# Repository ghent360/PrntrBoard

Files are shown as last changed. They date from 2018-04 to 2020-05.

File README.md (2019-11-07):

Prntr Board V1
======================
## *Deprecated*
**This project has run it's course. Most of the features are complete and there is little I can improve further. I have switched my focus to the [V2 design](https://github.com/ghent360/PrntrBoardV2).**

------------------

PrntrBoard is a 3D printer controller board designed to work with STM32 NUCLEO dev kits. The current version (V1) supports NUCLEO-64 series kits. The design is being developed on F446-RE kit, but other models could work as well. IMO the STM32F446 NUCLEO-64 kit offers very good performance (180MHz CPU) for the price ($15).

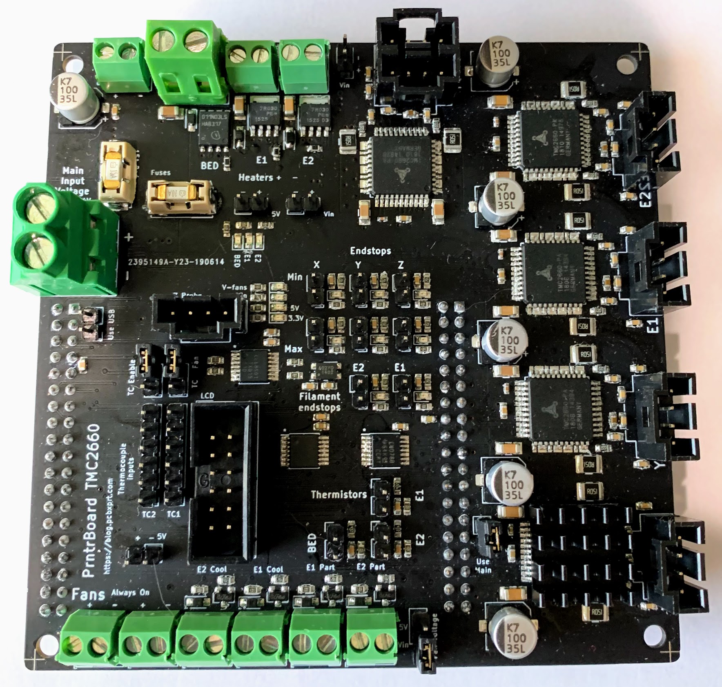
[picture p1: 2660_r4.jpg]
Picture of Rev2 Kicad Rendering

Some features of the board:
-----
  + 5x Trinamic super quiet drivers (TMC2130, TMC2660 or TMC2209)
  + Marlin 2.0 firmware
  + (2+2) controllable fans and 2x "always on" fan connectors
  + 3x min and max endstops for the x, y and z axis
  + 2x end stops for fillament end detection
  + SPI or I2C display connector for ST7735 or SSD1306 screen + one button and rotary encoder
  + Dual thermocouple connectors (for MAX31866, MAX31855 or MAX6675 boards)
  + Input voltage (Vin): 12-24V
  + selectable fan voltage (5V or Vin)

Because the NUCLEO-64 has limited number of IO pins, some compromises had to be made:
  + ~~No sd-card~~ (sd-card is added using new NUCLEO-64 compatible board)
  + The thermocouple connectors share pins with the E0 and E1 cool fan controls. You'll have to decide to use one or the other via jumpers on the board. Most printers I've seen come with "always on" extruder fans, the choice seemed like a worthy sacrifice.

Generic shortcuts I don't plan to improve:
------
  + ~~5V power supply is external. These are available from various resellers and fairly cheap - less than $1. No need to waste board layout space and component count.~~ (this has beed addresses with the new NUCLEO-64 compatible daugherboard)
  + Heated bed MOSFET - large heated beds consume a lot of power and it is challenging to provision the design for > 20A current (there is simply not enough copper space on the board to support this current). External heated bed MOSFETs are very affordable < $10 and support 20A-40A with no issues. If you have large heated bed - use external MOSFET or SSR.

Details
------
I use the daily build of KiCad (soon to be released V6) - let me know if you have trouble opening the files.

The current PCB desing is using 4 layer board, 6/6 mil track width/clearance, 12 mil min via hole size and 20 mil via diameter.

There are tree active branches:
  + tmc2130 - the board design for TMC2130 drivers
  + tmc2130-redesign - redesign of the TMC2130 branch with the nucleo board flipped
  + tmc2660 - the board design for TMC2660 drivers
  + tmc2209 - the board design for TMC2209 drivers

TMC2130 and TMC2660 PCB designs use the QFP version of the driver ICs, because they can handle a bit more power. The TMC2209 is available only in QFN package.

Status
------
TMC2130 version is table and been running for over a year. TMC2660 is being tested at the moment. Prototypes of the TMC2209 are being made.

old status:
I've been running a prototype of this board for a few months now and I'm very happy with the board stability. I'm trying to figure out how to make these at scale.

I have made prototypes of the TMC2130 board design (rev0) - the board has a few bugs, that are corrected in the rev1 version. Rev0 did not have LCD screen, it was added in Rev1. I'm trying to work-out the thermal design issues.
Rev1 board have been ordered and the dev branch is now switched to Rev2. The thermocouple connectors are added Rev2.
Rev2 borads have been ordered. The current working board is rev3. Added 2 more pins to the LCD connector
for the rotary encoder input. I also re-connected the E1 and E0 CS pins, so the LCD pins can be connected
to the hardware I2C pins. This way one can use SPI or I2C screens.

This branch is a redesign of the TMC2130 board. The main difference is that the NUCLEO board is flipped in a more natural position. In addition I'm now using a dedicated ground plane, larger heatsink areas for the mosfets. I'm much happier with the thermal layout of this branch.

The NUCLEO-64 board was limiting the design in many ways. I have a replacement board using STM32F407VE. This is 100 pin part. The new daughter board is the same form factor as the NUCLEO-64. It adds SPI EEPROM as well as native USB interface and micro SD-Card socket. The new board also has enough space for 24V to 5V buck converter, so power supply can beintegrated.

Tested circuits:
  + Heater control
  + Thermistor input
  + Fan control
  + Motor driver control
  + Z probe
  + End stops
  + Thermocuple interface (tested MAX31855 with Smoothieware)
  + LCD interface (tested REPRAP discount full graphics controller - the panel has issues
  sharing the SPI port with the TMC drivers. Could be solved with adapter board with extra AND gate)

Circuits that need verification:
  + Stall guard alert from the motor driver

Software
------

The software for the board is a clone of Marlin at [bugfix-2.0.x branch](https://github.com/ghent360/Marlin/tree/bugfix-2.0.x/ "Github.com") of my repository. It is quite usable. I keep it relatively in sync with the Marlin branch. *Note: there are other branches of Marlin, only the bugfix-2.0.x supports the STM32 microcontroller.*

Marlin is using Adruino IDE or Platform IO. I personally had issues with Platform IO not supporting the STM32F4 board, so I use Arduino version 1.8.5. To compile the firmware code you would need to install the [STM32 Arduino port](https://github.com/stm32duino/Arduino_Core_STM32 "www.stm32duino.com").

I'm also porting [Smoothieware](http://smoothieware.org) V1 to the board. So far I got the heater control and the stepper drivers working. My smoothie port is available [here](https://github.com/ghent360/Smoothieware-STM32F4 "Gitgub.com"). Please not the Smoothie port is not ready yet (there is an issue with the ADC). I have done only minimal tests so far.

Visit [my blog](https://blog.pcbxprt.com/) for status updates on the development of the board.

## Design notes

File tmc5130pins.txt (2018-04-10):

1 TST_MODE
2 CLK
3 ~CS
4 SCK
5 SDI
6 N/C
7 SDO
8 STEP
9 DIR
10 VCC_IO
11 SD_MODE
12 SPI_MODE
13 GNDP
14 N/C
15 OB1
16 N/C
17 BRB
18 N/C
19 OB2
20 N/C
21 VS
22 N/C
23 ENCN_DCO
24 ENDB_DCEN
25 ENCA_DCIN
26 DIAG0
27 DIAG1
28 SWSEL
29 DRV_ENN
30 AIN_REF
31 N/C
32 GNDA
33 5VOUT
34 VCC
35 CPO
36 N/C
37 CPI
38 VCP
39 VSA
40 VS
41 N/C
42 OA2
43 N/C
44 BRA
45 N/C
46 OA1
47 N/C
48 GNDP
49 PAD

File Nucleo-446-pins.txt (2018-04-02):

1 PC10
2 PC11
3 PC12
4 PD2
5 VDD
6 E5V
7 BOOT0
8 GND
9 NC
10 NC
11 NC
12 IOREF
13 PA13
14 ~RESET
15 PA14
16 3.3v
17 PA15
18 5V
19 GND
20 GND
21 PB7
22 GND
23 PC13
24 VIN
25 PC14
26 NC
27 PC15
28 PA0
29 PH0
30 PA1
31 PH1
32 PA4
33 VBAT
34 PB0
35 PC2
36 PC1
37 PC3
38 PC0
39 PC9
40 PC8
41 PB8
42 PC6
43 PB9
44 PC5
45 AVDD
46 U5V
47 GND
48 NC
49 PA5
50 PA12
51 PA6
52 PA11
53 PA7
54 PB12
55 PB6
56 NC
57 PC7
58 GND
59 PA9
60 PB2
61 PA8
62 PB1
63 PB10
64 PB15
65 PB4
66 PB14
67 PB5
68 PB13
69 PB3
70 AGND
71 PA10
72 PC4
73 PA2
74 NC
75 PA3
76 NC

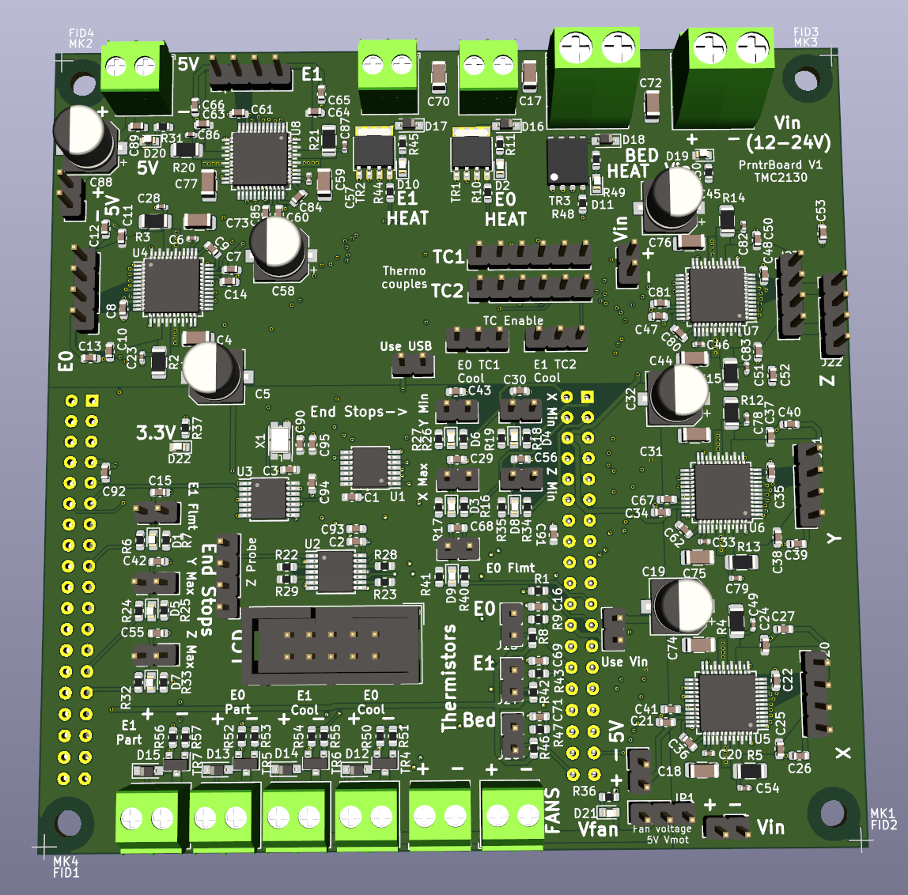
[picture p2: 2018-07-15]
Rev2_2.png

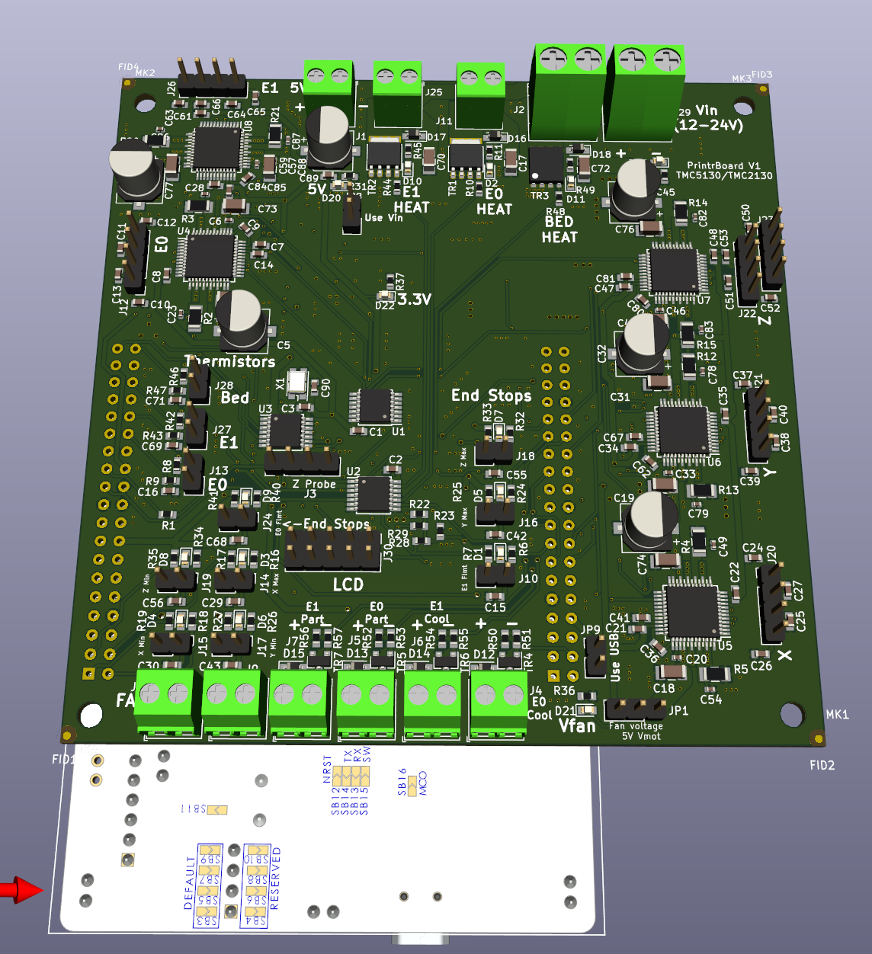
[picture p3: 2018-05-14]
Rev1_1.png

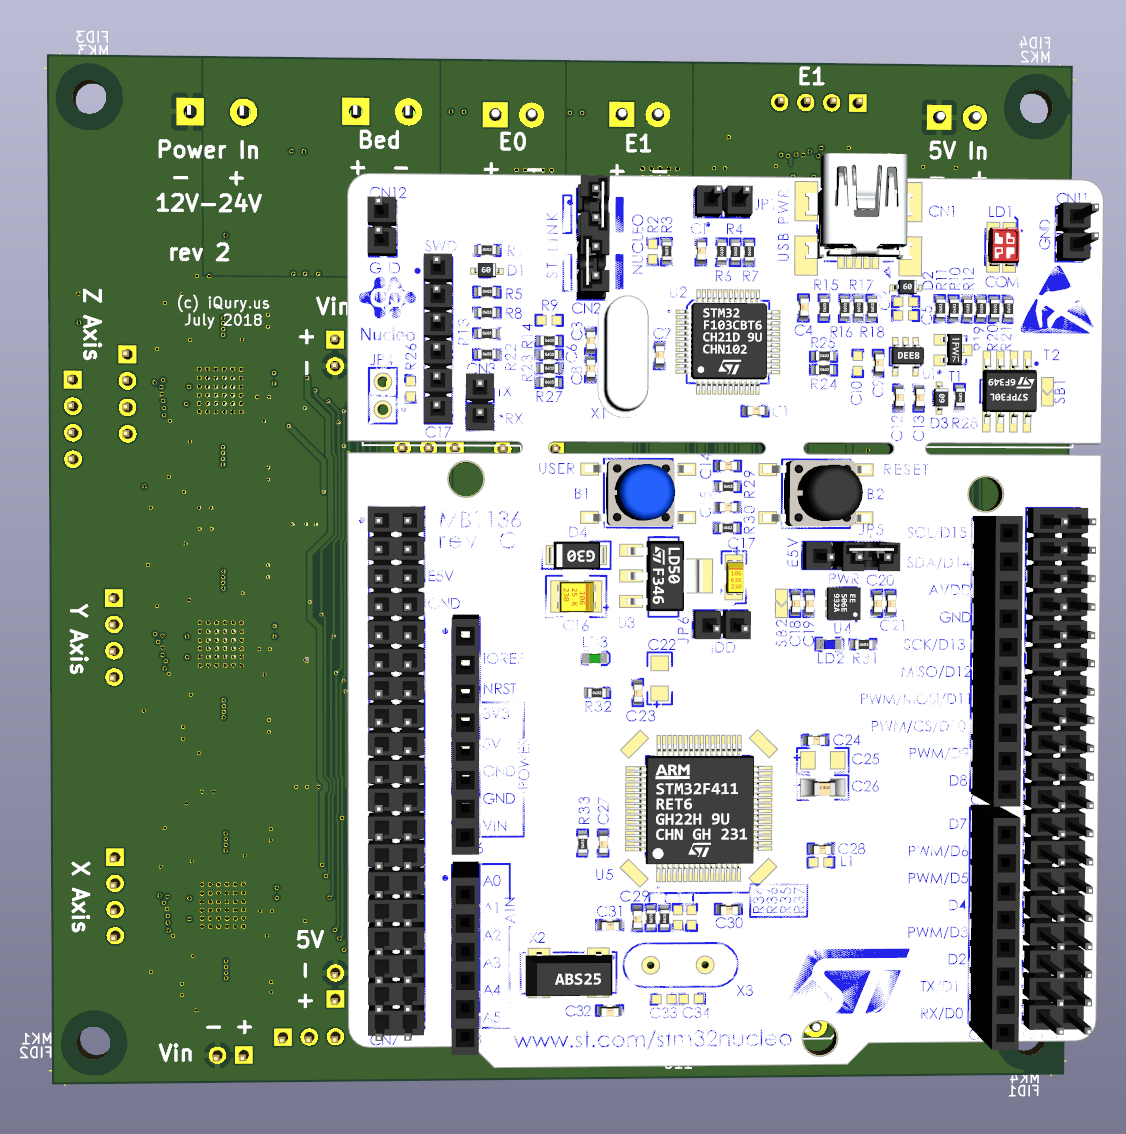
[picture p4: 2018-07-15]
Rev2_1.png

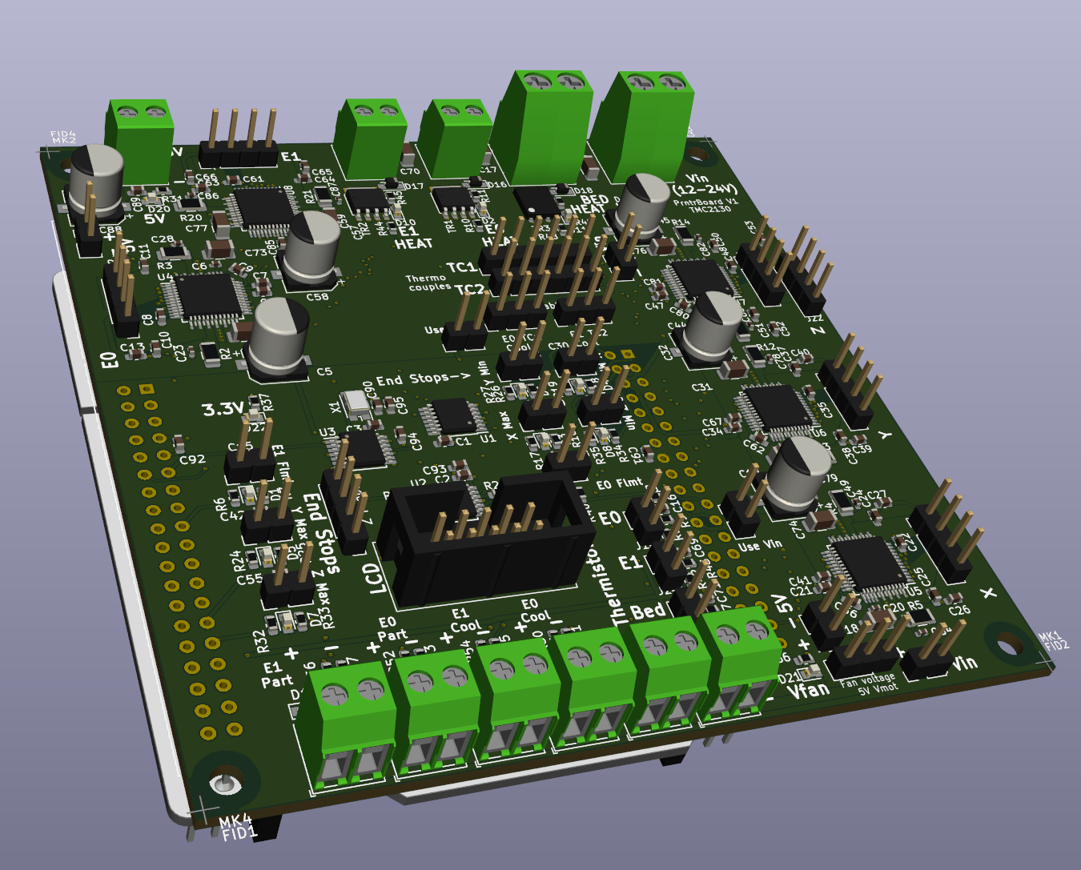
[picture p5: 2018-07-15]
Rev2_3.png

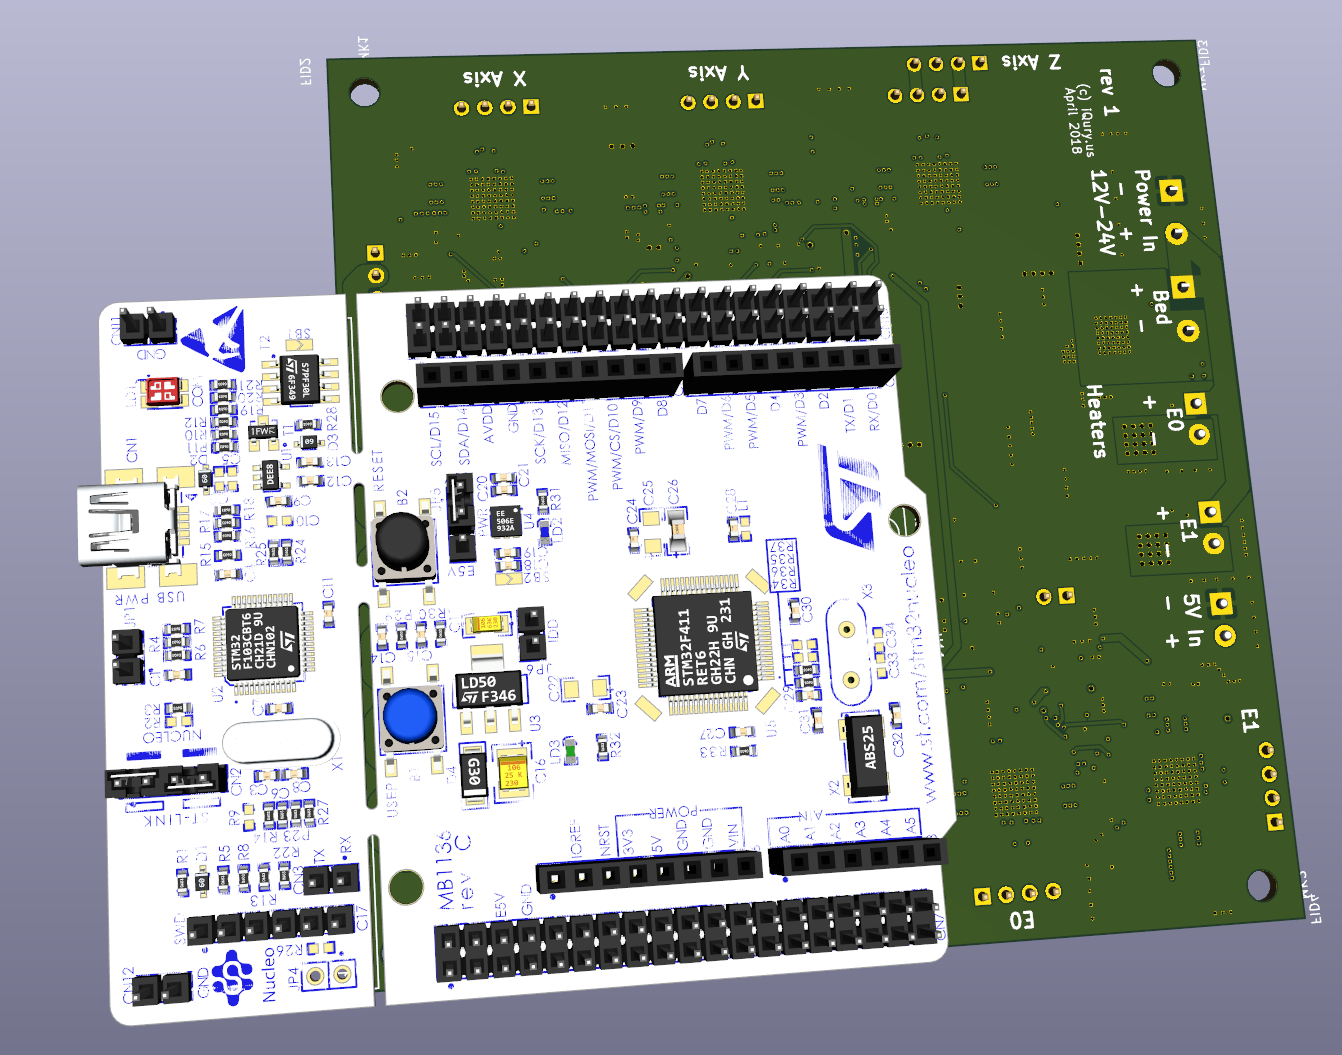
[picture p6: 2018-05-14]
Rev1_2.png

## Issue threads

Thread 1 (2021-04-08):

some advices

chinamore, 2021-04-08:
This version has the biggest problem. I guess no one except you dares to copy this board. My idea is very simple. You can clear all the TMC2660 and use a double-layer board layout, which will save a lot of cost. Provide 4 signals for each axis of the closed-loop printer: P+D+E+GND, which will greatly facilitate players who use external drives

ghent360, 2021-04-08:
Could you elaborate what problem you are referring to?
I do not believe a double layer board would provide sufficient cooling.
Also the cost difference of a double vs 4 layer board is minimal at 10x10cm
size (jlcpcb.com).

~V

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

M10CUBE, 2021-12-05:
Hi @ghent360
Some time ago we made a hardware platform called M10CUBE
https://hackaday.io/project/171770-m10cube
https://gitlab.com/m10cube/m10
A few days ago I ported to M10CUBE from maker @terjeio a similar to yours (NUCLEO64) hardware but for CNC control
https://github.com/terjeio/CNC_Breakout_Nucleo64/issues/3
I know you made a new version of the REPRAP controller but I like more the NUCLEO idea. More flexible and extremely cheap.
One goal now I am looking is to make a common controller for REPRAP and CNC.
Having all I/Os needed of the main board and use M10CUBE I/O modules

I have explained the concept here:
https://github.com/grblHAL/RP2040/discussions/3#discussioncomment-1752487
I am watching this in your you tube channel as well
Thanks

Since you are an experience designer I like to here from you if something like that makes sense to others as it makes sense to me.
Thank and congratulations for your grate designs.

ghent360, 2021-12-05:
Hi,

One drawback of the nucleo-style board is that a lot of space is wasted on
the I/O ports. Especially if you want to go to a 100-pin or larger MCU
package - the 2.4mm pin spacing eats a lot of space, so you will have to go
to a fancier connector with higher density, which unfortunately removes the
price advantages.

If you focus on CNC controls - they use a relatively small number of IO
lines. If you move to integrated stepper drivers (Trinamic or others) -
then you have to add SPI, UART and other pins and the 64-pin package is not
sufficient and at one point half your board is consumed by the
board-to-board interconnect. It is not an impossible problem to solve -
just something to keep in mind as you go along.

~V

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

M10CUBE, 2021-12-06:
Thanks @ghent360 for the quick response. All you said have solid ground. It is not a simple task to solve. For my M10CUBE concept to make sense is to make some compromises. So I end up thinking the cons and pros
CONS:
1 Some ARM modules are larger than M10CUBE format
2 The density of a design using the actual MPU chips  can not achieved in case of using some module incarnation. Using bare bone MPU chip is more dense but you loose the fun of reusing the plug in module.
3 Cost looks higher as well. I made the math.

PROS
1 - Construction in mind using ST Nucleo64 or Raspberry Pi Pico. That is ARM MPU, Cheep, Highly supported, Ready available and have room for next more powerful board announcements in the years to come. Probably these modules are found already in every serious maker.
2 - Fits nicely into M10CUBE concept (90X90 mm and up to 100X100 on the not fixed connectors side)
3 - Some space is lost because of the footage but on top has a lot of hardware impossible to make it on the footprint lost. On top of that you have the real estate underneath the module to place other hardware. In the end you gain more space than you loose
4 - Ready for Analog, Ethernet and Can Bus to experiment (I am sure the newcomer as well **I3C** or **the 10BASE-T1L Ethernet)**
5 - Extremely useful for the education community. That was the success of Raspberry (plus the clever engineering of course).
6 - All I/Os will move to an extra M10CUBE module so space on board only used for step drivers (encoder inputs under consideration). I will stic on SPI interface for trinamic and not UART but still I need discrete signals 6XStep/Dir/Enable as maker @terjeiro from GRBLHAL stated.
7 - ...more to come

That is to build a common board for GRBL and MAPLIN as I state it here:
https://github.com/grblHAL/RP2040/discussions/3#discussioncomment-1752835

The design is not cure for ever illnesses  but a "medicine" to cure many and become a useful tool for makers and educational community. So any info and help is valuable to me

Thanks

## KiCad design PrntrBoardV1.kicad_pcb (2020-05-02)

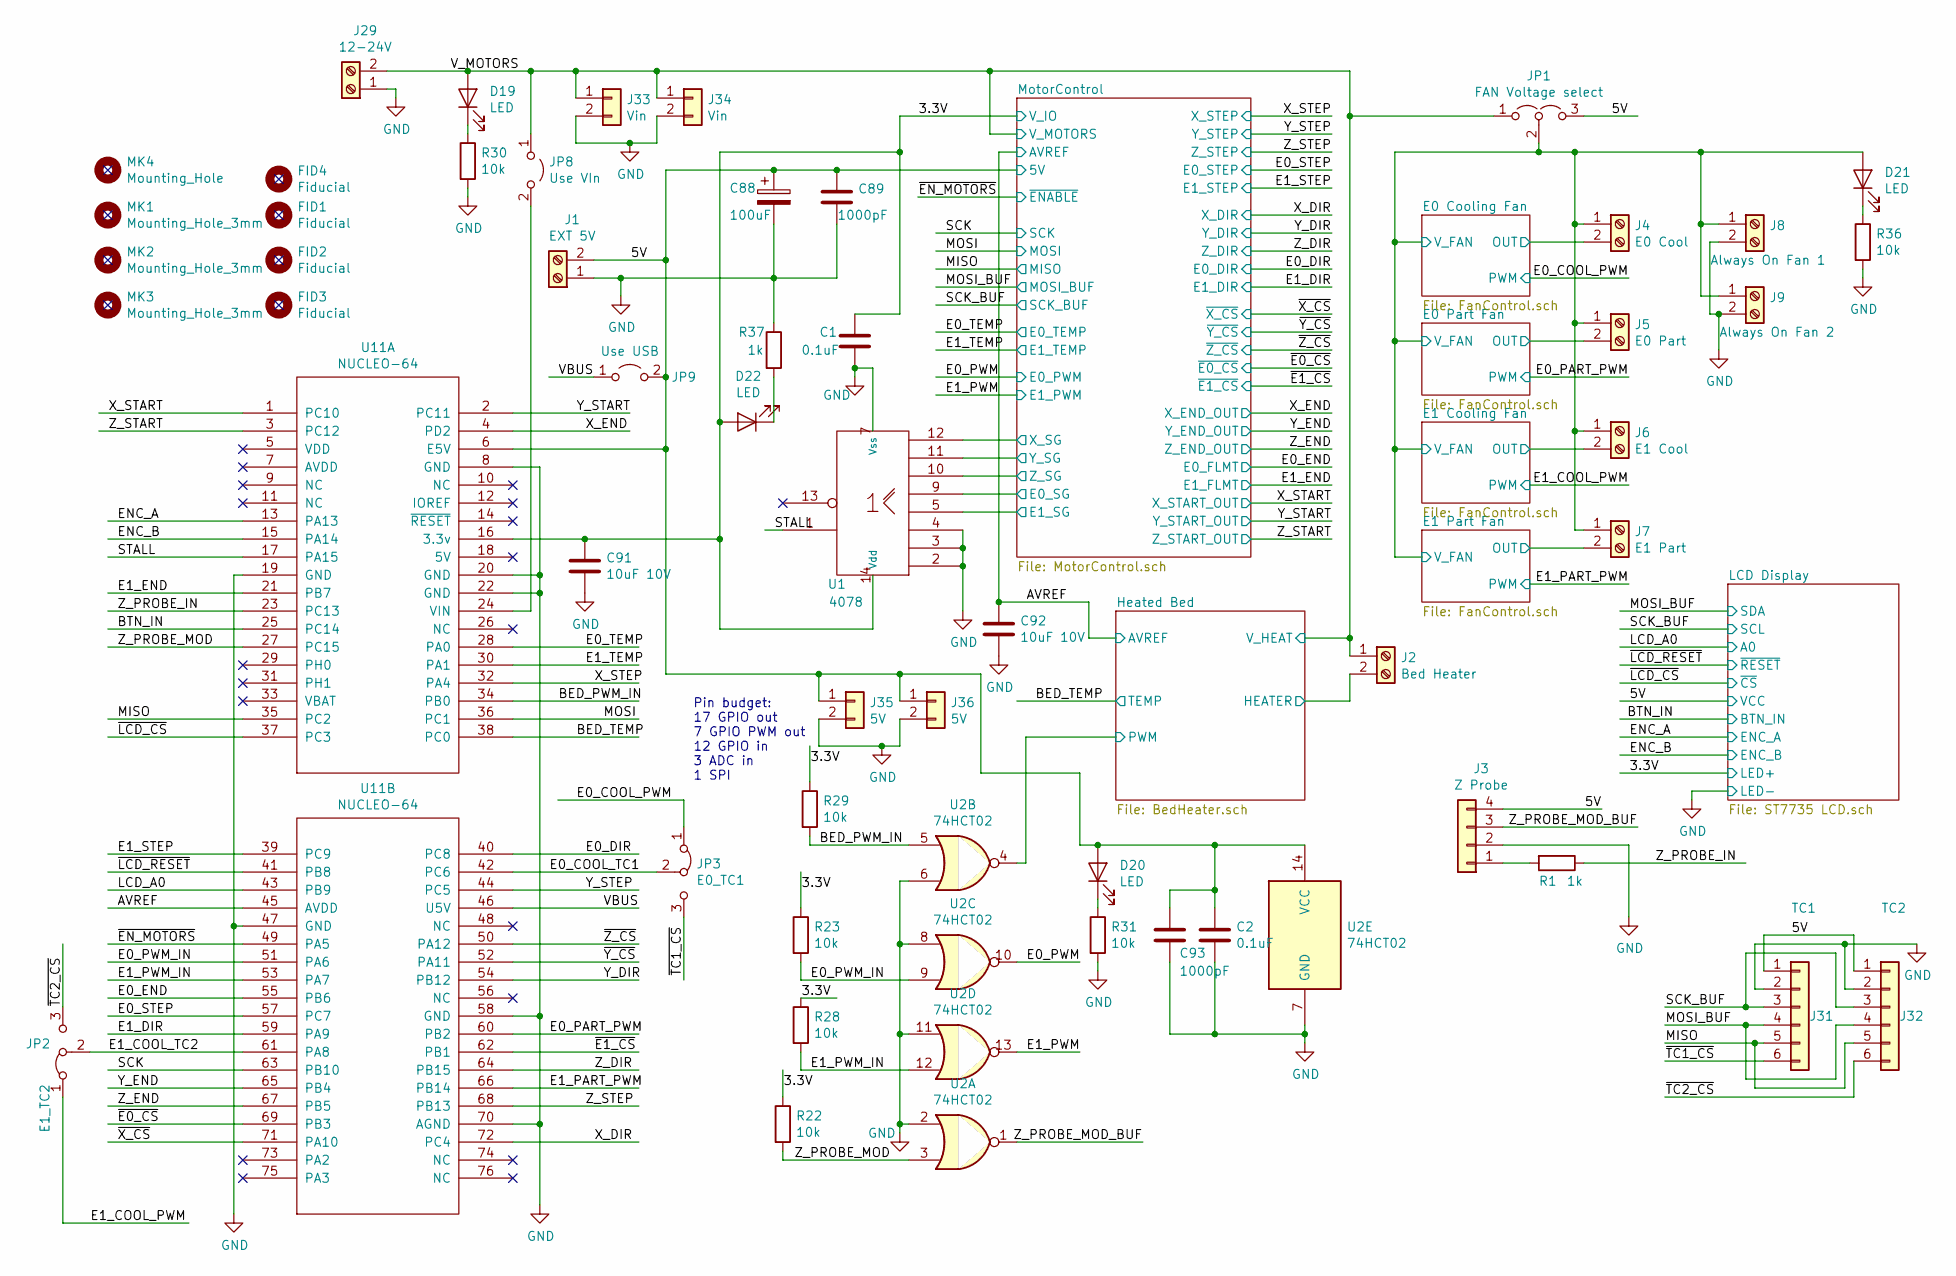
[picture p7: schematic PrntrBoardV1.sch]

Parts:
C1, C2: 0.1uF; C_0603_1608Metric
C88: 100uF; CP_Elec_6.3x7.7
C89, C93: 1000pF; C_0603_1608Metric
C91, C92: 10uF 10V; C_0603_1608Metric
D19, D20, D21, D22: LED; LED_0603_1608Metric
FID1, FID2, FID3, FID4: Fiducial; Fiducial_1mm_Dia_2.54mm_Outer_CopperTop
J1: EXT 5V; TerminalBlock_Phoenix_PT-1,5-2-3.5-H_1x02_P3.50mm_Horizontal
J2: Bed Heater; TerminalBlock_Phoenix_MKDS-1,5-2-5.08_1x02_P5.08mm_Horizont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
J3: Z Probe; PinHeader_1x04_P2.54mm_Vertical
J4: E0 Cool; TerminalBlock_Phoenix_PT-1,5-2-3.5-H_1x02_P3.50mm_Horizontal
J5: E0 Part; TerminalBlock_Phoenix_PT-1,5-2-3.5-H_1x02_P3.50mm_Horizontal
J6: E1 Cool; TerminalBlock_Phoenix_PT-1,5-2-3.5-H_1x02_P3.50mm_Horizontal
J7: E1 Part; TerminalBlock_Phoenix_PT-1,5-2-3.5-H_1x02_P3.50mm_Horizontal
J8: Always On Fan 1; TerminalBlock_Phoenix_PT-1,5-2-3.5-H_1x02_P3.50mm_Horizontal
J9: Always On Fan 2; TerminalBlock_Phoenix_PT-1,5-2-3.5-H_1x02_P3.50mm_Horizontal
J29: 12-24V; TerminalBlock_MetzConnect_Type701_RT11L02HGLU_1x02_P6.35mm_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
J31: TC1; PinHeader_1x06_P2.54mm_Vertical
J32: TC2; PinHeader_1x06_P2.54mm_Vertical
J33, J34: Vin; PinHeader_1x02_P2.54mm_Vertical
J35, J36: 5V; PinHeader_1x02_P2.54mm_Vertical
JP1: FAN Voltage select; PinHeader_1x03_P2.54mm_Vertical
JP2: E1_TC2; PinHeader_1x03_P2.54mm_Vertical
JP3: E0_TC1; PinHeader_1x03_P2.54mm_Vertical
JP8: Use VIn; PinHeader_1x02_P2.54mm_Vertical
JP9: Use USB; PinHeader_1x02_P2.54mm_Vertical
MK1, MK2, MK3: Mounting_Hole_3mm; MountingHole_3.2mm_M3
MK4: Mounting_Hole; MountingHole_3.2mm_M3
R1, R37: 1k; R_0603_1608Metric
R22, R23, R28, R29, R30, R31, R36: 10k; R_0603_1608Metric
U1: 4078; TSSOP-14_4.4x5mm_P0.65mm
U2: 74HCT02; TSSOP-14_4.4x5mm_P0.65mm
U11: NUCLEO-64; Nucleo-64

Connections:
/3.3V: C1.1, C91.1, D22.2 (A), R22.1, R23.1, R28.1, R29.1, U1.14 (Vdd), U11.16 (3.3v); also elsewhere on the board
/5V: C2.1, C88.1, C89.1, C93.1, D20.2 (A), J1.2, J3.4, J31.1, J32.1, J35.1, J36.1, JP1.3 (B), JP9.2 (B), U2.14 (VCC), U11.6 (E5V); also elsewhere on the board
/AVREF: C92.1, U11.45 (AVDD); also elsewhere on the board
/BED_PWM_IN: R29.2, U2.5, U11.34 (PB0)
/BED_TEMP: U11.38 (PC0); also elsewhere on the board
/BTN_IN: U11.25 (PC14); also elsewhere on the board
/E0_COOL_PWM: JP3.1 (A); also elsewhere on the board
/E0_COOL_TC1: JP3.2 (C), U11.42 (PC6)
/E0_DIR: U11.40 (PC8); also elsewhere on the board
/E0_END: U11.55 (PB6); also elsewhere on the board
/E0_PART_PWM: U11.60 (PB2); also elsewhere on the board
/E0_PWM: U2.10; also elsewhere on the board
/E0_PWM_IN: R23.2, U2.9, U11.51 (PA6)
/E0_SG: U1.9; also elsewhere on the board
/E0_STEP: U11.57 (PC7); also elsewhere on the board
/E0_TEMP: U11.28 (PA0); also elsewhere on the board
/E1_COOL_PWM: JP2.1 (A); also elsewhere on the board
/E1_COOL_TC2: JP2.2 (C), U11.61 (PA8)
/E1_DIR: U11.59 (PA9); also elsewhere on the board
/E1_END: U11.21 (PB7); also elsewhere on the board
/E1_PART_PWM: U11.66 (PB14); also elsewhere on the board
/E1_PWM: U2.13; also elsewhere on the board
/E1_PWM_IN: R28.2, U2.12, U11.53 (PA7)
/E1_SG: U1.5; also elsewhere on the board
/E1_STEP: U11.39 (PC9); also elsewhere on the board
/E1_TEMP: U11.30 (PA1); also elsewhere on the board
/ENC_A: U11.13 (PA13); also elsewhere on the board
/ENC_B: U11.15 (PA14); also elsewhere on the board
/LCD_A0: U11.43 (PB9); also elsewhere on the board
/MISO: J31.5, J32.5, U11.35 (PC2); also elsewhere on the board
/MOSI: U11.36 (PC1); also elsewhere on the board
/MOSI_BUF: J31.4, J32.4; also elsewhere on the board
/OUT: J4.2; also elsewhere on the board
/OUT_1: J7.2; also elsewhere on the board
/OUT_2: J5.2; also elsewhere on the board
/OUT_3: J6.2; also elsewhere on the board
/PWM: U2.4; also elsewhere on the board
/SCK: U11.63 (PB10); also elsewhere on the board
/SCK_BUF: J31.3, J32.3; also elsewhere on the board
/STALL: U1.1, U11.17 (PA15)
/VBUS: JP9.1 (A), U11.46 (U5V)
/V_FAN: D21.2 (A), J4.1, J5.1, J6.1, J7.1, J8.1, J9.1, JP1.2 (C); also elsewhere on the board
/V_MOTORS: D19.2 (A), J2.1, J29.2, J33.1, J34.1, JP1.1 (A), JP8.1 (A); also elsewhere on the board
/X_DIR: U11.72 (PC4); also elsewhere on the board
/X_END: U11.4 (PD2); also elsewhere on the board
/X_SG: U1.12; also elsewhere on the board
/X_START: U11.1 (PC10); also elsewhere on the board
/X_STEP: U11.32 (PA4); also elsewhere on the board
/Y_DIR: U11.54 (PB12); also elsewhere on the board
/Y_END: U11.65 (PB4); also elsewhere on the board
/Y_SG: U1.11; also elsewhere on the board
/Y_START: U11.2 (PC11); also elsewhere on the board
/Y_STEP: U11.44 (PC5); also elsewhere on the board
/Z_DIR: U11.64 (PB15); also elsewhere on the board
/Z_END: U11.67 (PB5); also elsewhere on the board
/Z_PROBE_IN: R1.1, U11.23 (PC13)
/Z_PROBE_MOD: R22.2, U2.3, U11.27 (PC15)
/Z_PROBE_MOD_BUF: J3.3, U2.1
/Z_SG: U1.10; also elsewhere on the board
/Z_START: U11.3 (PC12); also elsewhere on the board
/Z_STEP: U11.68 (PB13); also elsewhere on the board
/~E0_CS: U11.69 (PB3); also elsewhere on the board
/~E1_CS: U11.62 (PB1); also elsewhere on the board
/~EN_MOTORS: U11.49 (PA5); also elsewhere on the board
/~LCD_CS: U11.37 (PC3); also elsewhere on the board
/~LCD_RESET: U11.41 (PB8); also elsewhere on the board
/~TC1_CS: J31.6, JP3.3 (B)
/~TC2_CS: J32.6, JP2.3 (B)
/~X_CS: U11.71 (PA10); also elsewhere on the board
/~Y_CS: U11.52 (PA11); also elsewhere on the board
/~Z_CS: U11.50 (PA12); also elsewhere on the board
GND: C1.2, C2.2, C88.2, C89.2, C91.2, C92.2, C93.2, J1.1, J3.2, J8.2, J9.2, J29.1, J31.2, J32.2, J33.2, J34.2, J35.2, J36.2, R30.2, R31.2, R36.2, R37.1, U1.2, U1.3, U1.4, U1.7 (Vss), U2.2, U2.6, U2.7 (GND), U2.8, U2.11, U11.8 (GND), U11.19 (GND), U11.20 (GND), U11.22 (GND), U11.47 (GND), U11.58 (GND), U11.70 (AGND); also elsewhere on the board
unnamed: D19.1 (K), R30.1
unnamed: D20.1 (K), R31.1
unnamed: D21.1 (K), R36.1
unnamed: D22.1 (K), R37.2
unnamed: J3.1, R1.2
unnamed: JP8.2 (B), U11.24 (VIN)

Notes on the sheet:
Pin budget: 17 GPIO out 7 GPIO PWM out 12 GPIO in 3 ADC in 1 SPI

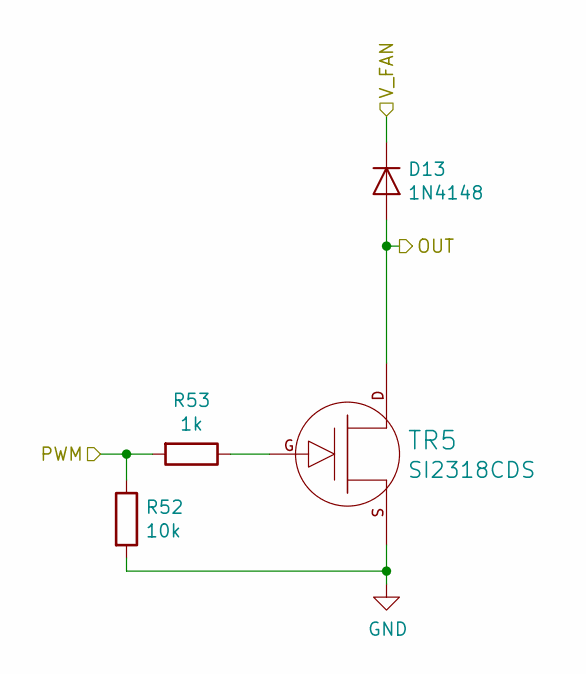
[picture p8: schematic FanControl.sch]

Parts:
D12: 1N4148; D_SOD-323_HandSoldering
R50: 10k; R_0603_1608Metric
R51: 1k; R_0603_1608Metric
TR4: SI2318CDS; SOT-23

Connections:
/E0_COOL_PWM: R50.1, R51.2; also elsewhere on the board
/OUT: D12.2 (A), TR4.D; also elsewhere on the board
/V_FAN: D12.1 (K); also elsewhere on the board
GND: R50.2, TR4.S; also elsewhere on the board
unnamed: R51.1, TR4.G

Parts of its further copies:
D13, D14, D15: 1N4148; D_SOD-323_HandSoldering
R52, R54, R56: 10k; R_0603_1608Metric
R53, R55, R57: 1k; R_0603_1608Metric
TR5, TR6, TR7: SI2318CDS; SOT-23

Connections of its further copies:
/E0_PART_PWM: R52.1, R53.2; also elsewhere on the board
/E1_COOL_PWM: R54.1, R55.2; also elsewhere on the board
/E1_PART_PWM: R56.1, R57.2; also elsewhere on the board
/OUT_1: D15.2 (A), TR7.D; also elsewhere on the board
/OUT_2: D13.2 (A), TR5.D; also elsewhere on the board
/OUT_3: D14.2 (A), TR6.D; also elsewhere on the board
/V_FAN: D13.1 (K), D14.1 (K), D15.1 (K); also elsewhere on the board
GND: R52.2, R54.2, R56.2, TR5.S, TR6.S, TR7.S; also elsewhere on the board
unnamed: R53.1, TR5.G
unnamed: R55.1, TR6.G
unnamed: R57.1, TR7.G

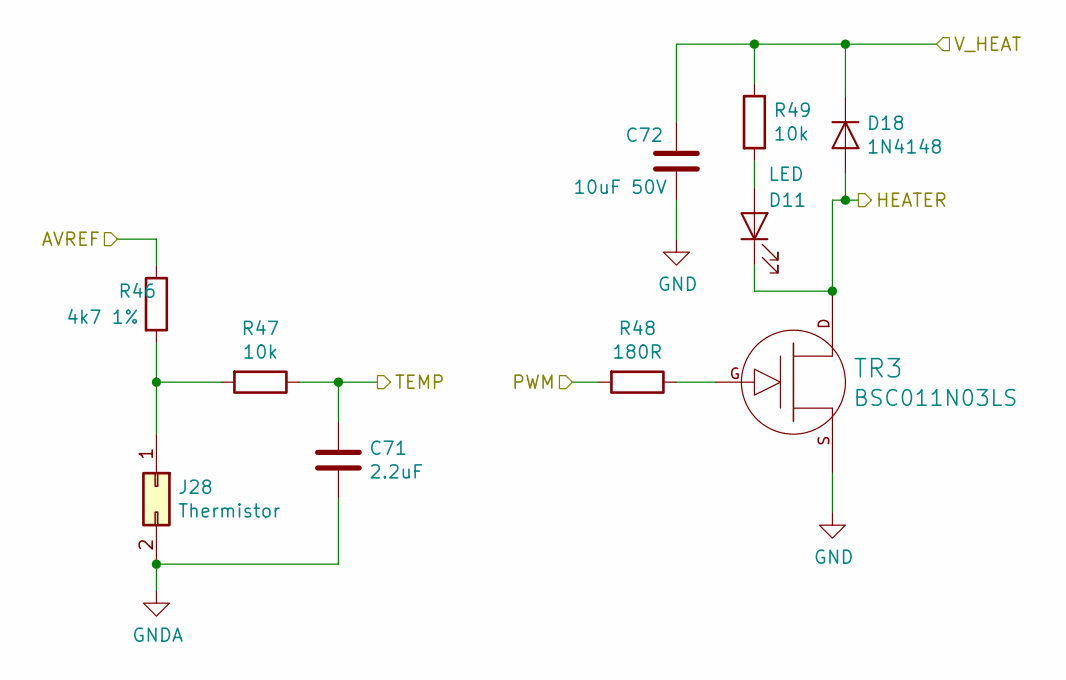
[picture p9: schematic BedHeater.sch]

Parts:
C16: 2.2uF; C_0603_1608Metric
C17: 10uF 50V; C_1206_3216Metric
D2: LED; LED_0603_1608Metric
D18: 1N4148; D_SOD-323_HandSoldering
J13: Thermistor; PinHeader_1x02_P2.54mm_Vertical
R8: 4k7 1%; R_0603_1608Metric
R9, R11: 10k; R_0603_1608Metric
R10: 180R; R_0603_1608Metric
TR1: BSC011N03LS; PG-TDSON-8-FL

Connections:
/AVREF: R8.1; also elsewhere on the board
/E0_PWM: R10.2; also elsewhere on the board
/E0_TEMP: C16.1, R9.1; also elsewhere on the board
/V_MOTORS: C17.1, D18.1 (K), R11.1; also elsewhere on the board
GND: C16.2, C17.2, J13.2, TR1.S; also elsewhere on the board
unnamed: D2.2 (A), R11.2
unnamed: J13.1, R8.2, R9.2
unnamed: R10.1, TR1.G

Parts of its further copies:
C69, C71: 2.2uF; C_0603_1608Metric
C70, C72: 10uF 50V; C_1206_3216Metric
D10, D11: LED; LED_0603_1608Metric
J27, J28: Thermistor; PinHeader_1x02_P2.54mm_Vertical
R42, R46: 4k7 1%; R_0603_1608Metric
R43, R45, R47, R49: 10k; R_0603_1608Metric
R44, R48: 180R; R_0603_1608Metric
TR3: BSC011N03LS; PG-TDSON-8-FL

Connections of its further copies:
/AVREF: R42.1, R46.1; also elsewhere on the board
/BED_TEMP: C71.1, R47.1; also elsewhere on the board
/E1_PWM: R44.2; also elsewhere on the board
/E1_TEMP: C69.1, R43.1; also elsewhere on the board
/PWM: R48.2; also elsewhere on the board
/V_MOTORS: C70.1, C72.1, R45.1, R49.1; also elsewhere on the board
GND: C69.2, C70.2, C71.2, C72.2, J27.2, J28.2, TR3.S; also elsewhere on the board
unnamed: D10.2 (A), R45.2
unnamed: D11.2 (A), R49.2
unnamed: J27.1, R42.2, R43.2
unnamed: J28.1, R46.2, R47.2
unnamed 145: R44.1; also elsewhere on the board
unnamed: R48.1, TR3.G

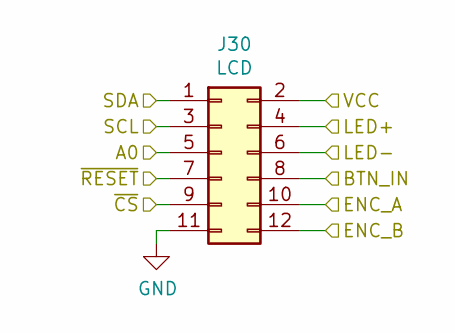
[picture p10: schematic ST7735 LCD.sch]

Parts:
J30: LCD; IDC-Header_2x06_P2.54mm_Vertical

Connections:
/3.3V: J30.4; also elsewhere on the board
/5V: J30.2; also elsewhere on the board
/BTN_IN: J30.8; also elsewhere on the board
/ENC_A: J30.10; also elsewhere on the board
/ENC_B: J30.12; also elsewhere on the board
/LCD_A0: J30.5; also elsewhere on the board
/MOSI_BUF: J30.1; also elsewhere on the board
/SCK_BUF: J30.3; also elsewhere on the board
/~LCD_CS: J30.9; also elsewhere on the board
/~LCD_RESET: J30.7; also elsewhere on the board
GND: J30.6, J30.11; also elsewhere on the board

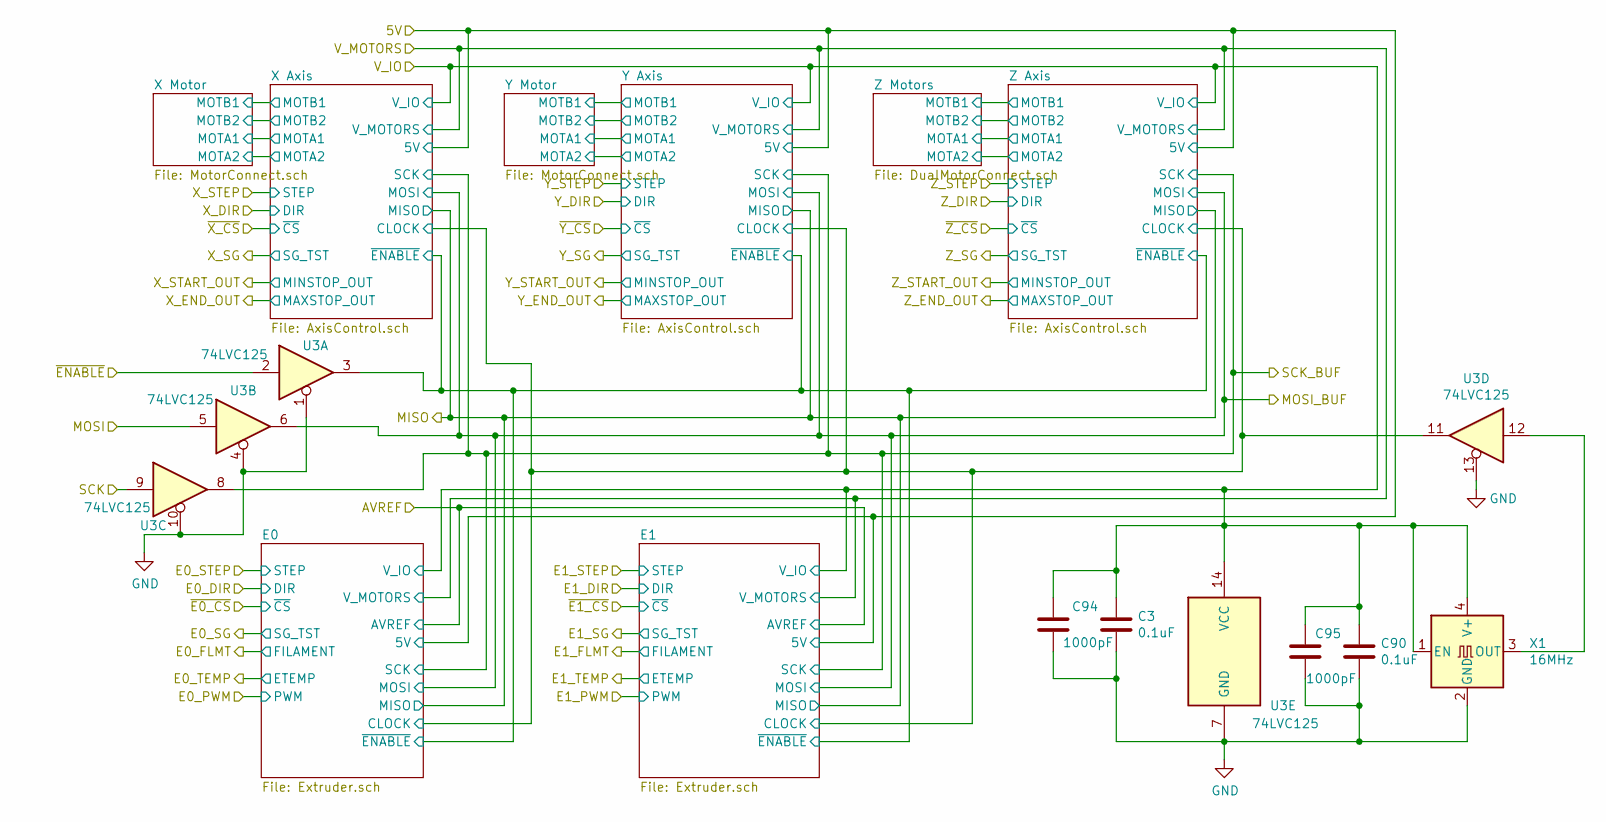
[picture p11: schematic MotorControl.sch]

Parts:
C3, C90: 0.1uF; C_0603_1608Metric
C94, C95: 1000pF; C_0603_1608Metric
U3: 74LVC125; TSSOP-14_4.4x5mm_P0.65mm
X1: 16MHz; Oscillator_SMD_EuroQuartz_XO32-4Pin_3.2x2.5mm_HandSoldering

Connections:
/3.3V: C3.1, C90.1, C94.1, C95.1, U3.14 (VCC), X1.1 (EN), X1.4 (V+); also elsewhere on the board
/MOSI: U3.5; also elsewhere on the board
/MOSI_BUF: U3.6; also elsewhere on the board
/MotorControl/CLOCK: U3.11; also elsewhere on the board
/MotorControl/~ENABLE_1: U3.3; also elsewhere on the board
/SCK: U3.9; also elsewhere on the board
/SCK_BUF: U3.8; also elsewhere on the board
/~EN_MOTORS: U3.2; also elsewhere on the board
GND: C3.2, C90.2, C94.2, C95.2, U3.1, U3.4, U3.7 (GND), U3.10, U3.13, X1.2 (GND); also elsewhere on the board
unnamed: U3.12, X1.3 (OUT)

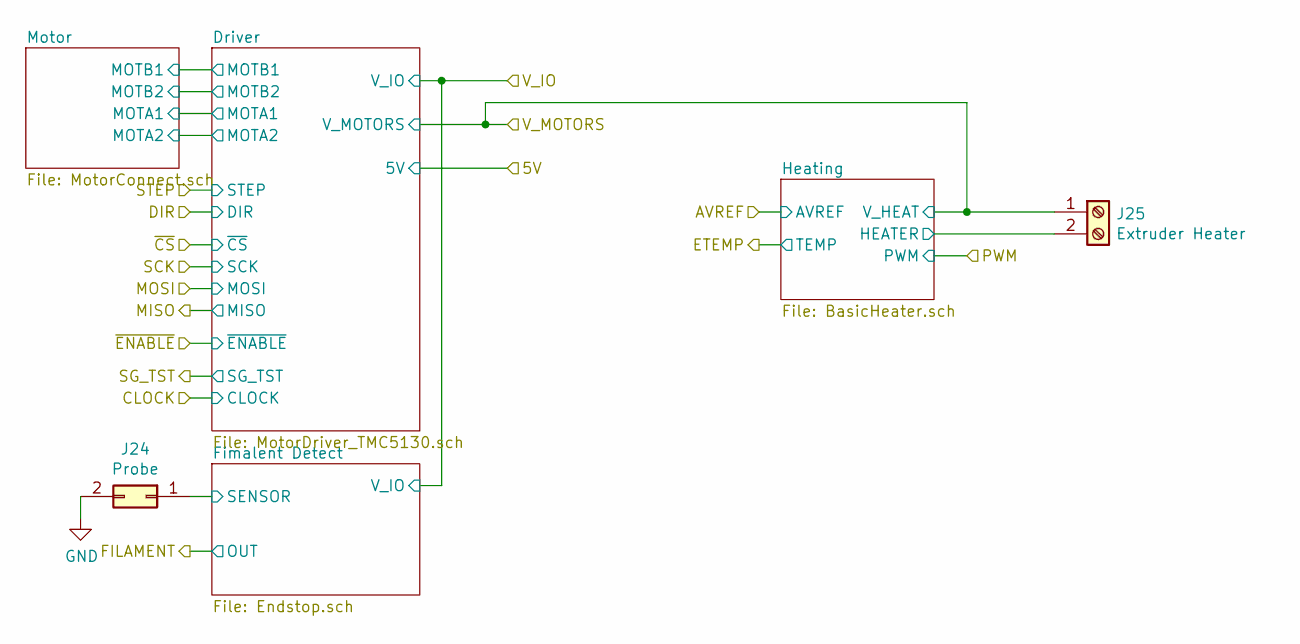
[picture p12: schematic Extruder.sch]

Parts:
J10: Probe; PinHeader_1x02_P2.54mm_Vertical
J11: Extruder Heater; TerminalBlock_Phoenix_PT-1,5-2-3.5-H_1x02_P3.50mm_Horizontal

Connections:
/MotorControl/E0/SENSOR: J10.1; also elsewhere on the board
/V_MOTORS: J11.1; also elsewhere on the board
GND: J10.2; also elsewhere on the board

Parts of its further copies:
J24: Probe; PinHeader_1x02_P2.54mm_Vertical
J25: Extruder Heater; TerminalBlock_Phoenix_PT-1,5-2-3.5-H_1x02_P3.50mm_Horizontal

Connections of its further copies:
/MotorControl/E1/SENSOR: J24.1; also elsewhere on the board
/V_MOTORS: J25.1; also elsewhere on the board
GND: J24.2; also elsewhere on the board

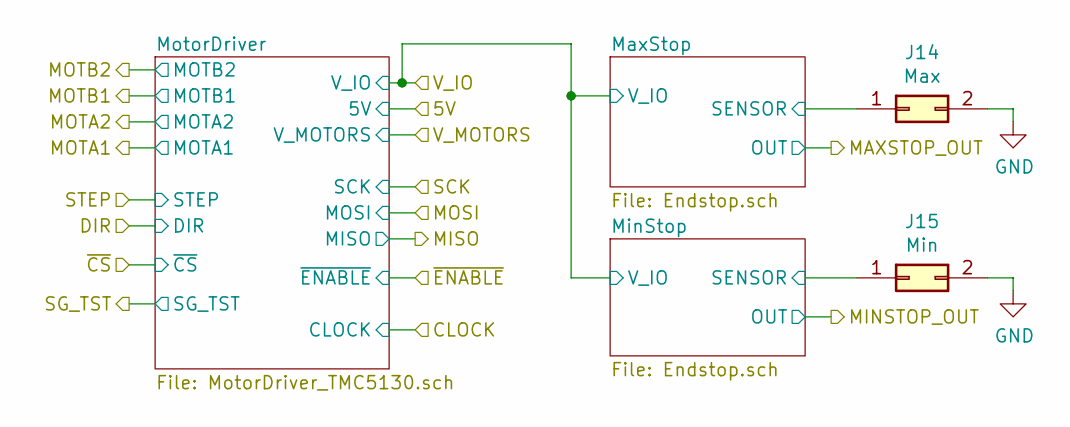
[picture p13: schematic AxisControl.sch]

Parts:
J14: Max; PinHeader_1x02_P2.54mm_Vertical
J15: Min; PinHeader_1x02_P2.54mm_Vertical

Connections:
/MotorControl/X Axis/SENSOR: J14.1; also elsewhere on the board
/MotorControl/X Axis/SENSOR_1: J15.1; also elsewhere on the board
GND: J14.2, J15.2; also elsewhere on the board

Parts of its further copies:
J16, J18: Max; PinHeader_1x02_P2.54mm_Vertical
J17, J19: Min; PinHeader_1x02_P2.54mm_Vertical

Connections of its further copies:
/MotorControl/Y Axis/SENSOR: J16.1; also elsewhere on the board
/MotorControl/Y Axis/SENSOR_1: J17.1; also elsewhere on the board
/MotorControl/Z Axis/SENSOR: J18.1; also elsewhere on the board
/MotorControl/Z Axis/SENSOR_1: J19.1; also elsewhere on the board
GND: J16.2, J17.2, J18.2, J19.2; also elsewhere on the board

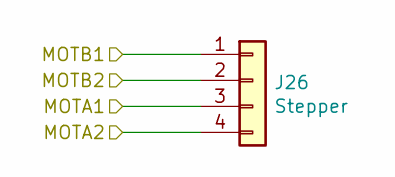
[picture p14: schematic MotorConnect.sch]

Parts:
J12: Stepper; PinHeader_1x04_P2.54mm_Vertical

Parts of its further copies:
J20, J21, J22, J23, J26: Stepper; PinHeader_1x04_P2.54mm_Vertical

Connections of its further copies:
/MotorControl/MOTA1: J20.3; also elsewhere on the board
/MotorControl/MOTA1_1: J23.3; also elsewhere on the board
/MotorControl/MOTA1_2: J21.3; also elsewhere on the board
/MotorControl/MOTA2: J20.4; also elsewhere on the board
/MotorControl/MOTA2_1: J22.4; also elsewhere on the board
/MotorControl/MOTA2_2: J21.4; also elsewhere on the board
/MotorControl/MOTB1: J20.1; also elsewhere on the board
/MotorControl/MOTB1_1: J23.1; also elsewhere on the board
/MotorControl/MOTB1_2: J21.1; also elsewhere on the board
/MotorControl/MOTB2: J20.2; also elsewhere on the board
/MotorControl/MOTB2_1: J22.2; also elsewhere on the board
/MotorControl/MOTB2_2: J21.2; also elsewhere on the board
/MotorControl/Z Motors/MOTA1_1: J22.3, J23.4
/MotorControl/Z Motors/MOTB2_1: J22.1, J23.2

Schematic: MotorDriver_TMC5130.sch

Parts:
C4, C74: 10uF 50V; C_1206_3216Metric
C5: 100uF 35V; CP_Elec_6.3x7.7
C6, C86, C87: 0.1uF 50V; C_0402_1005Metric
C7: 0.47uF; C_0603_1608Metric
C8, C85: 0.1uF; C_0603_1608Metric
C10, C11, C12, C13: 1000pF; C_0603_1608Metric
C84: 0.022uF 50V; C_0603_1608Metric
R20, R21: 0R15 0.5W; R_1206_3216Metric
U8: TMC5130; tmc5130-nc

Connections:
/3.3V: C8.1, U8.10 (VCC_IO); also elsewhere on the board
/5V: C7.2, U8.34 (VCC); also elsewhere on the board
/E1_DIR: U8.9 (DIR); also elsewhere on the board
/E1_SG: U8.27 (DIAG1); also elsewhere on the board
/E1_STEP: U8.8 (STEP); also elsewhere on the board
/MISO: U8.7 (SDO); also elsewhere on the board
/MOSI_BUF: U8.5 (SDI); also elsewhere on the board
/MotorControl/CLOCK: U8.2 (CLK); also elsewhere on the board
/MotorControl/~ENABLE_1: U8.29 (~ENABLE); also elsewhere on the board
/SCK_BUF: U8.4 (SCK); also elsewhere on the board
/V_MOTORS: C4.1, C5.1, C6.1, C74.1, U8.21 (VS), U8.39 (VSA), U8.40 (VS); also elsewhere on the board
/~E1_CS: U8.3 (~CS); also elsewhere on the board
GND: C4.2, C5.2, C7.1, C8.2, C10.1, C11.1, C12.1, C13.1, C74.2, C85.1, C86.2, C87.2, R20.2, R21.2, U8.1 (TST_MODE), U8.6 (N/C), U8.13 (GNDP), U8.24 (ENDB_DCEN), U8.31 (N/C), U8.32 (GNDA), U8.36 (N/C), U8.48 (GNDP), U8.49 (PAD); also elsewhere on the board
unnamed: C84.1, U8.37 (CPI)
unnamed: C84.2, U8.35 (CPO)
unnamed: C85.2, U8.33 (5VOUT)
unnamed: C86.1, R20.1, U8.17 (BRB)
unnamed: C87.1, R21.1, U8.44 (BRA)

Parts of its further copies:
C9, C36, C62, C80: 0.022uF 50V; C_0603_1608Metric
C14, C22, C35, C41, C48, C61, C67, C81: 0.1uF; C_0603_1608Metric
C18, C31, C44, C57, C73, C75, C76, C77: 10uF 50V; C_1206_3216Metric
C19, C32, C45, C58: 100uF 35V; CP_Elec_6.3x7.7
C20, C23, C28, C33, C46, C49, C54, C59, C78, C79, C82, C83: 0.1uF 50V; C_0402_1005Metric
C21, C34, C47, C60: 0.47uF; C_0603_1608Metric
C24, C25, C26, C27, C37, C38, C39, C40, C50, C51, C52, C53, C63, C64, C65, C66: 1000pF; C_0603_1608Metric
R2, R3, R4, R5, R12, R13, R14, R15: 0R15 0.5W; R_1206_3216Metric
U4, U5, U6, U7: TMC5130; tmc5130-nc

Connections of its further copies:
/3.3V: C22.1, C35.1, C48.1, C61.1, U4.10 (VCC_IO), U5.10 (VCC_IO), U6.10 (VCC_IO), U7.10 (VCC_IO); also elsewhere on the board
/5V: C21.2, C34.2, C47.2, C60.2, U4.34 (VCC), U5.34 (VCC), U6.34 (VCC), U7.34 (VCC); also elsewhere on the board
/E0_DIR: U4.9 (DIR); also elsewhere on the board
/E0_SG: U4.27 (DIAG1); also elsewhere on the board
/E0_STEP: U4.8 (STEP); also elsewhere on the board
/MISO: U4.7 (SDO), U5.7 (SDO), U6.7 (SDO), U7.7 (SDO); also elsewhere on the board
/MOSI_BUF: U4.5 (SDI), U5.5 (SDI), U6.5 (SDI), U7.5 (SDI); also elsewhere on the board
/MotorControl/CLOCK: U4.2 (CLK), U5.2 (CLK), U6.2 (CLK), U7.2 (CLK); also elsewhere on the board
/MotorControl/MOTA1: C25.2, U5.46 (OA1); also elsewhere on the board
/MotorControl/MOTA1_1: C51.2, U7.46 (OA1); also elsewhere on the board
/MotorControl/MOTA1_2: C38.2, U6.46 (OA1); also elsewhere on the board
/MotorControl/MOTA2: C26.2, U5.42 (OA2); also elsewhere on the board
/MotorControl/MOTA2_1: C52.2, U7.42 (OA2); also elsewhere on the board
/MotorControl/MOTA2_2: C39.2, U6.42 (OA2); also elsewhere on the board
/MotorControl/MOTB1: C24.2, U5.15 (OB1); also elsewhere on the board
/MotorControl/MOTB1_1: C50.2, U7.15 (OB1); also elsewhere on the board
/MotorControl/MOTB1_2: C37.2, U6.15 (OB1); also elsewhere on the board
/MotorControl/MOTB2: C27.2, U5.19 (OB2); also elsewhere on the board
/MotorControl/MOTB2_1: C53.2, U7.19 (OB2); also elsewhere on the board
/MotorControl/MOTB2_2: C40.2, U6.19 (OB2); also elsewhere on the board
/MotorControl/~ENABLE_1: U4.29 (~ENABLE), U5.29 (~ENABLE), U6.29 (~ENABLE), U7.29 (~ENABLE); also elsewhere on the board
/SCK_BUF: U4.4 (SCK), U5.4 (SCK), U6.4 (SCK), U7.4 (SCK); also elsewhere on the board
/V_MOTORS: C18.1, C19.1, C20.1, C31.1, C32.1, C33.1, C44.1, C45.1, C46.1, C57.1, C58.1, C59.1, C73.1, C75.1, C76.1, C77.1, U4.21 (VS), U4.39 (VSA), U4.40 (VS), U5.21 (VS), U5.39 (VSA), U5.40 (VS), U6.21 (VS), U6.39 (VSA), U6.40 (VS), U7.21 (VS), U7.39 (VSA), U7.40 (VS); also elsewhere on the board
/X_DIR: U5.9 (DIR); also elsewhere on the board
/X_SG: U5.27 (DIAG1); also elsewhere on the board
/X_STEP: U5.8 (STEP); also elsewhere on the board
/Y_DIR: U6.9 (DIR); also elsewhere on the board
/Y_SG: U6.27 (DIAG1); also elsewhere on the board
/Y_STEP: U6.8 (STEP); also elsewhere on the board
/Z_DIR: U7.9 (DIR); also elsewhere on the board
/Z_SG: U7.27 (DIAG1); also elsewhere on the board
/Z_STEP: U7.8 (STEP); also elsewhere on the board
/~E0_CS: U4.3 (~CS); also elsewhere on the board
/~X_CS: U5.3 (~CS); also elsewhere on the board
/~Y_CS: U6.3 (~CS); also elsewhere on the board
/~Z_CS: U7.3 (~CS); also elsewhere on the board
GND: C14.1, C18.2, C19.2, C21.1, C22.2, C23.2, C24.1, C25.1, C26.1, C27.1, C28.2, C31.2, C32.2, C34.1, C35.2, C37.1, C38.1, C39.1, C40.1, C41.1, C44.2, C45.2, C47.1, C48.2, C49.2, C50.1, C51.1, C52.1, C53.1, C54.2, C57.2, C58.2, C60.1, C61.2, C63.1, C64.1, C65.1, C66.1, C67.1, C73.2, C75.2, C76.2, C77.2, C78.2, C79.2, C81.1, C82.2, C83.2, R2.2, R3.2, R4.2, R5.2, R12.2, R13.2, R14.2, R15.2, U4.1 (TST_MODE), U4.6 (N/C), U4.13 (GNDP), U4.24 (ENDB_DCEN), U4.31 (N/C), U4.32 (GNDA), U4.36 (N/C), U4.48 (GNDP), U4.49 (PAD), U5.1 (TST_MODE), U5.6 (N/C), U5.13 (GNDP), U5.24 (ENDB_DCEN), U5.31 (N/C), U5.32 (GNDA), U5.36 (N/C), U5.48 (GNDP), U5.49 (PAD), U6.1 (TST_MODE), U6.6 (N/C), U6.13 (GNDP), U6.24 (ENDB_DCEN), U6.31 (N/C), U6.32 (GNDA), U6.36 (N/C), U6.48 (GNDP), U6.49 (PAD), U7.1 (TST_MODE), U7.6 (N/C), U7.13 (GNDP), U7.24 (ENDB_DCEN), U7.31 (N/C), U7.32 (GNDA), U7.36 (N/C), U7.48 (GNDP), U7.49 (PAD); also elsewhere on the board
unnamed: C9.1, U4.37 (CPI)
unnamed: C9.2, U4.35 (CPO)
unnamed: C14.2, U4.33 (5VOUT)
unnamed: C20.2, U5.38 (VCP)
unnamed: C23.1, R2.1, U4.17 (BRB)
unnamed: C28.1, R3.1, U4.44 (BRA)
unnamed: C33.2, U6.38 (VCP)
unnamed: C36.1, U5.37 (CPI)
unnamed: C36.2, U5.35 (CPO)
unnamed: C41.2, U5.33 (5VOUT)
unnamed: C46.2, U7.38 (VCP)
unnamed: C49.1, R4.1, U5.17 (BRB)
unnamed: C54.1, R5.1, U5.44 (BRA)
unnamed: C62.1, U6.37 (CPI)
unnamed: C62.2, U6.35 (CPO)
unnamed: C67.2, U6.33 (5VOUT)
unnamed: C78.1, R12.1, U6.17 (BRB)
unnamed: C79.1, R13.1, U6.44 (BRA)
unnamed: C80.1, U7.37 (CPI)
unnamed: C80.2, U7.35 (CPO)
unnamed: C81.2, U7.33 (5VOUT)
unnamed: C82.1, R14.1, U7.17 (BRB)
unnamed: C83.1, R15.1, U7.44 (BRA)

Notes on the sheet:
1000pf capacitors min 50V rating

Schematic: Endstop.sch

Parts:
C15: 1000pF; C_0603_1608Metric
D1: LED; LED_0603_1608Metric
R6: 10k; R_0603_1608Metric
R7: 1k; R_0603_1608Metric

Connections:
/3.3V: R7.1; also elsewhere on the board
/E0_END: R6.1; also elsewhere on the board
/MotorControl/E0/SENSOR: C15.1, D1.1 (K), R6.2; also elsewhere on the board
GND: C15.2; also elsewhere on the board
unnamed: D1.2 (A), R7.2

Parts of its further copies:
C29, C30, C42, C43, C55, C56, C68: 1000pF; C_0603_1608Metric
D3, D4, D5, D6, D7, D8, D9: LED; LED_0603_1608Metric
R16, R18, R24, R26, R32, R34, R40: 10k; R_0603_1608Metric
R17, R19, R25, R27, R33, R35, R41: 1k; R_0603_1608Metric

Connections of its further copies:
/3.3V: R17.1, R19.1, R25.1, R27.1, R33.1, R35.1, R41.1; also elsewhere on the board
/E1_END: R40.1; also elsewhere on the board
/MotorControl/E1/SENSOR: C68.1, D9.1 (K), R40.2; also elsewhere on the board
/MotorControl/X Axis/SENSOR: C29.1, D3.1 (K), R16.2; also elsewhere on the board
/MotorControl/X Axis/SENSOR_1: C30.1, D4.1 (K), R18.2; also elsewhere on the board
/MotorControl/Y Axis/SENSOR: C42.1, D5.1 (K), R24.2; also elsewhere on the board
/MotorControl/Y Axis/SENSOR_1: C43.1, D6.1 (K), R26.2; also elsewhere on the board
/MotorControl/Z Axis/SENSOR: C55.1, D7.1 (K), R32.2; also elsewhere on the board
/MotorControl/Z Axis/SENSOR_1: C56.1, D8.1 (K), R34.2; also elsewhere on the board
/X_END: R16.1; also elsewhere on the board
/X_START: R18.1; also elsewhere on the board
/Y_END: R24.1; also elsewhere on the board
/Y_START: R26.1; also elsewhere on the board
/Z_END: R32.1; also elsewhere on the board
/Z_START: R34.1; also elsewhere on the board
GND: C29.2, C30.2, C42.2, C43.2, C55.2, C56.2, C68.2; also elsewhere on the board
unnamed: D3.2 (A), R17.2
unnamed: D4.2 (A), R19.2
unnamed: D5.2 (A), R25.2
unnamed: D6.2 (A), R27.2
unnamed: D7.2 (A), R33.2
unnamed: D8.2 (A), R35.2
unnamed: D9.2 (A), R41.2

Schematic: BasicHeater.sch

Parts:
C16: 2.2uF; C_0603_1608Metric
C17: 10uF 50V; C_1206_3216Metric
D2: LED; LED_0603_1608Metric
D17: 1N4148; D_SOD-323_HandSoldering
J13: Thermistor; PinHeader_1x02_P2.54mm_Vertical
R8: 4k7 1%; R_0603_1608Metric
R9, R11: 10k; R_0603_1608Metric
R10: 180R; R_0603_1608Metric
TR1: PSMN7R0-30YL; SOT-669_LFPAK

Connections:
/AVREF: R8.1; also elsewhere on the board
/E0_PWM: R10.2; also elsewhere on the board
/E0_TEMP: C16.1, R9.1; also elsewhere on the board
/V_MOTORS: C17.1, D17.1 (K), R11.1; also elsewhere on the board
GND: C16.2, C17.2, J13.2, TR1.S; also elsewhere on the board
unnamed: D2.2 (A), R11.2
unnamed: J13.1, R8.2, R9.2
unnamed: R10.1, TR1.G

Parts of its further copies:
C69, C71: 2.2uF; C_0603_1608Metric
C70, C72: 10uF 50V; C_1206_3216Metric
D10, D11: LED; LED_0603_1608Metric
D16: 1N4148; D_SOD-323_HandSoldering
J27, J28: Thermistor; PinHeader_1x02_P2.54mm_Vertical
R42, R46: 4k7 1%; R_0603_1608Metric
R43, R45, R47, R49: 10k; R_0603_1608Metric
R44, R48: 180R; R_0603_1608Metric
TR2: PSMN7R0-30YL; SOT-669_LFPAK

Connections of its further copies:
/AVREF: R42.1, R46.1; also elsewhere on the board
/BED_TEMP: C71.1, R47.1; also elsewhere on the board
/E1_PWM: R44.2; also elsewhere on the board
/E1_TEMP: C69.1, R43.1; also elsewhere on the board
/PWM: R48.2; also elsewhere on the board
/V_MOTORS: C70.1, C72.1, D16.1 (K), R45.1, R49.1; also elsewhere on the board
GND: C69.2, C70.2, C71.2, C72.2, J27.2, J28.2, TR2.S; also elsewhere on the board
unnamed: D10.2 (A), R45.2
unnamed: D11.2 (A), R49.2
unnamed: J27.1, R42.2, R43.2
unnamed: J28.1, R46.2, R47.2
unnamed: R44.1, TR2.G
unnamed 146: R48.1; also elsewhere on the board

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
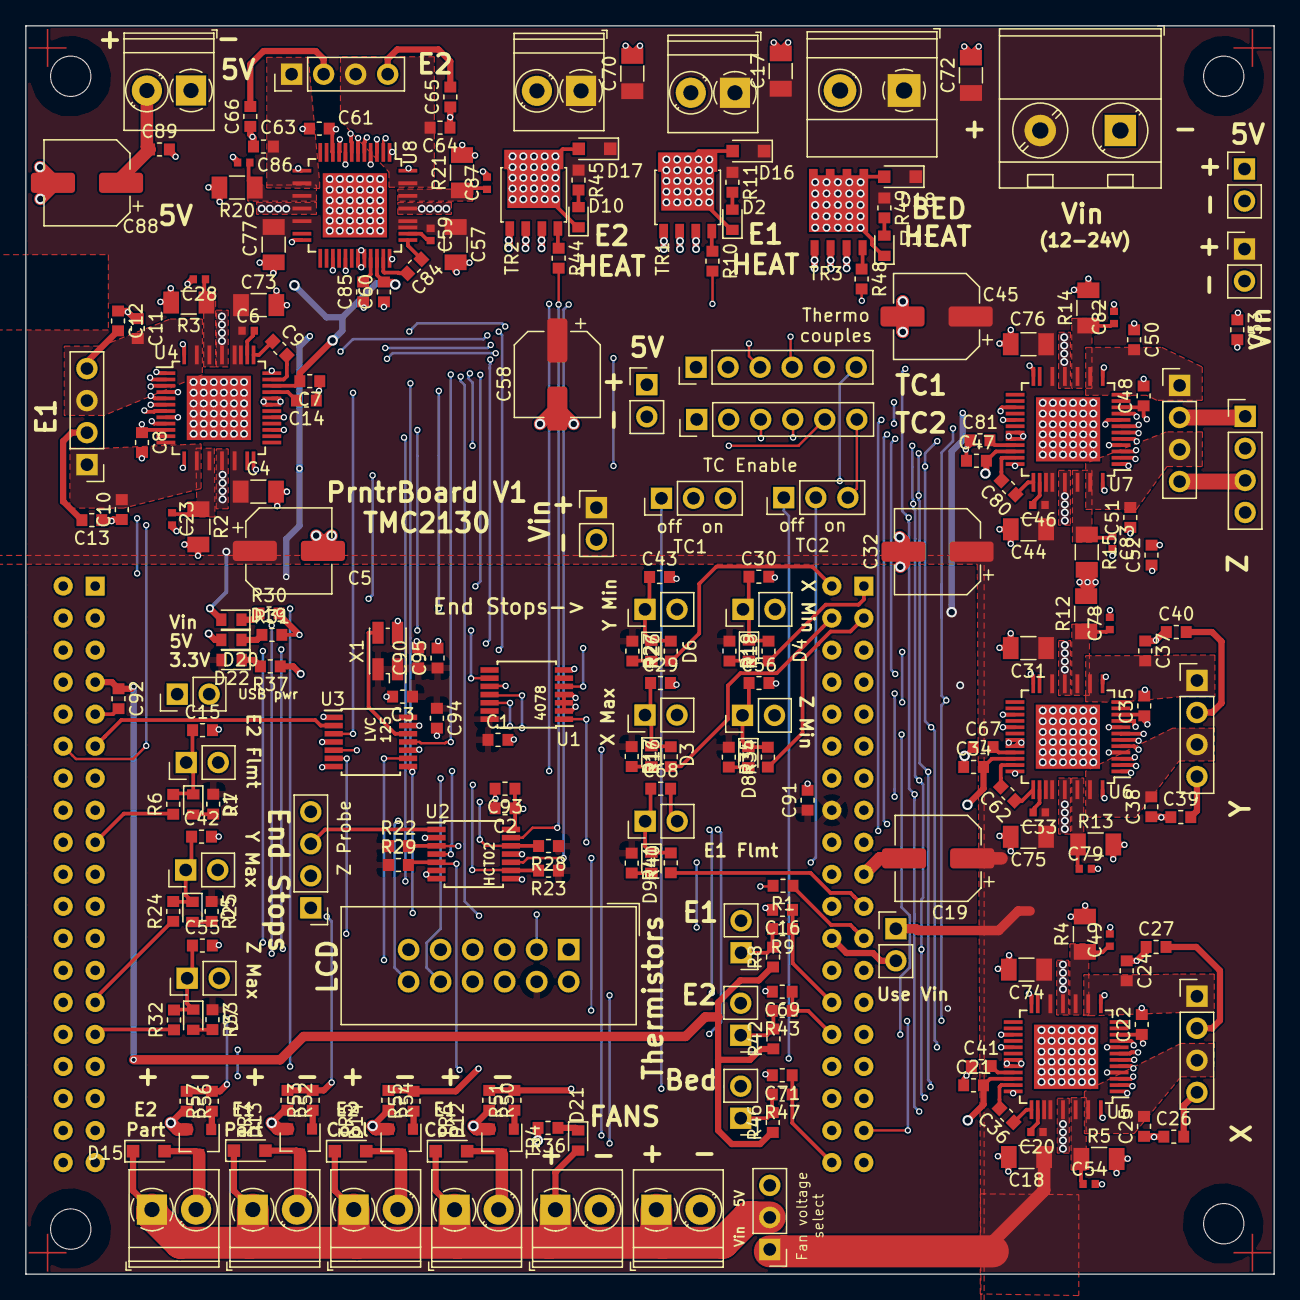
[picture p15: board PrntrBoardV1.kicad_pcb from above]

Board: 4 copper layers, 99.0 x 99.0 mm, 238 parts (1 on the bottom side), 165 nets.

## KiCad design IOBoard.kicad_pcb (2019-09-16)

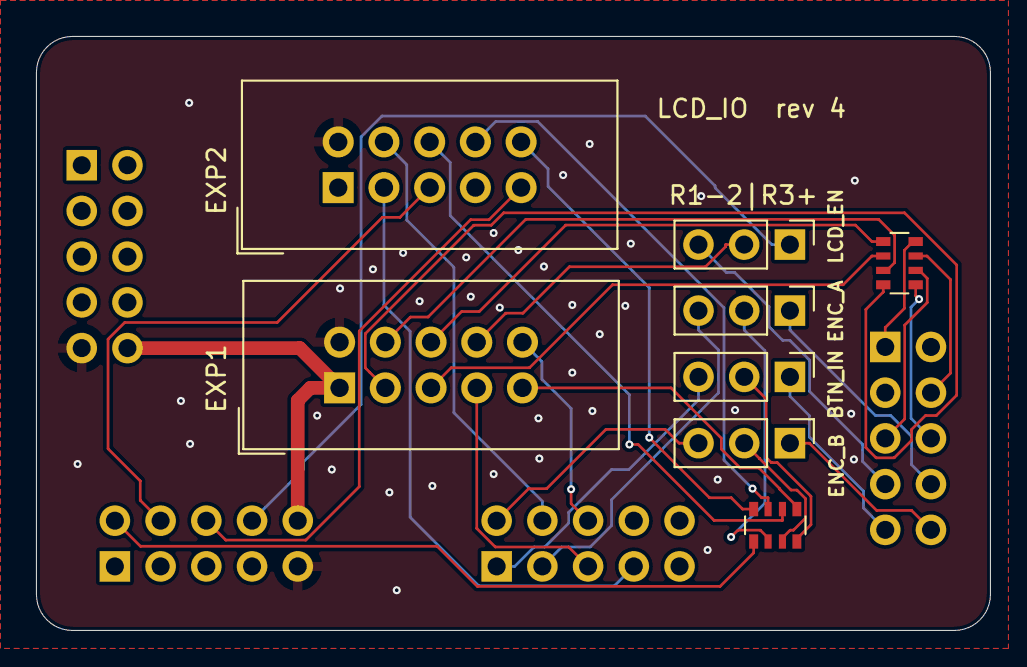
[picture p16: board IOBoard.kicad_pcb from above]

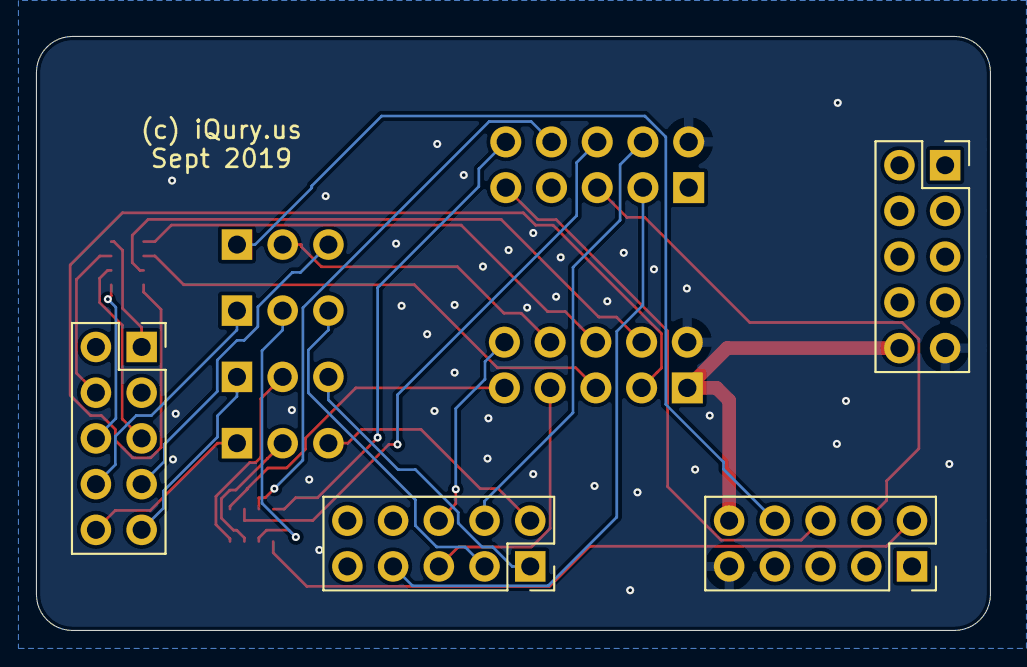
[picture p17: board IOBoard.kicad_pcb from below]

Board: 2 copper layers, 53.0 x 33.0 mm, 12 parts (4 on the bottom side), 33 nets.

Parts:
J1: EXP1; PinSocket_2x05_P2.54mm_Vertical
J2: EXP2; PinSocket_2x05_P2.54mm_Vertical
J3: LCD_EXP1; IDC-Header_2x05_P2.54mm_Vertical
J4: LCD_EXP2; IDC-Header_2x05_P2.54mm_Vertical
J5: EXP3; PinSocket_2x05_P2.54mm_Vertical
J6: EXP4; PinSocket_2x05_P2.54mm_Vertical
JP1: JP_BTN_IN; PinHeader_1x03_P2.54mm_Vertical
JP2: JP_ENC_B; PinHeader_1x03_P2.54mm_Vertical
JP3: JP_ENC_A; PinHeader_1x03_P2.54mm_Vertical
JP4: JP_LCD_EN; PinHeader_1x03_P2.54mm_Vertical
RN1, RN2: 4x10k; R_Array_Convex_4x0603

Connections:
/5V: J3.1, J5.10, J6.10
/BTN_ENC: J3.9, RN1.1
/BTN_IN: J2.9, JP1.1
/ENC_A: J2.8, JP3.1
/ENC_B: J2.10, JP2.1
/ENC_EN1: J4.8, RN1.3
/ENC_EN2: J4.6, RN1.2
/IOA_3: J2.1, RN2.8
/IOA_6: J2.4, RN2.7
/IOA_7: J2.5, RN2.6
/IOA_8: J2.6, RN2.5
/IOA_15: J2.7, JP4.3
/IOE_0: J1.1, JP1.3
/IOE_1: J1.2, JP2.3
/IOE_2: J1.3, JP3.3
/IOE_3: J1.4, J4.4
/IOE_4: J1.5, J3.7
/IOE_5: J1.6, J3.10
/IOE_6: J1.7, J4.3
/LCD_D4: J3.6, RN2.1
/LCD_D5: J3.5, RN2.2
/LCD_D6: J3.4, RN2.3
/LCD_D7: J3.3, RN2.4
/LCD_EN: J3.8, JP4.2
/MISO_IN: J4.10, RN1.4
/SPI2_MISO: J5.2, RN1.5
/SPI2_MOSI: J4.5, J5.4
/SPI2_SCK: J4.9, J5.6
/~LCD_CS: J5.8, JP4.1
GND: J3.2, J4.2, J5.9, J6.9
unnamed: JP1.2, RN1.8
unnamed: JP2.2, RN1.7
unnamed: JP3.2, RN1.6

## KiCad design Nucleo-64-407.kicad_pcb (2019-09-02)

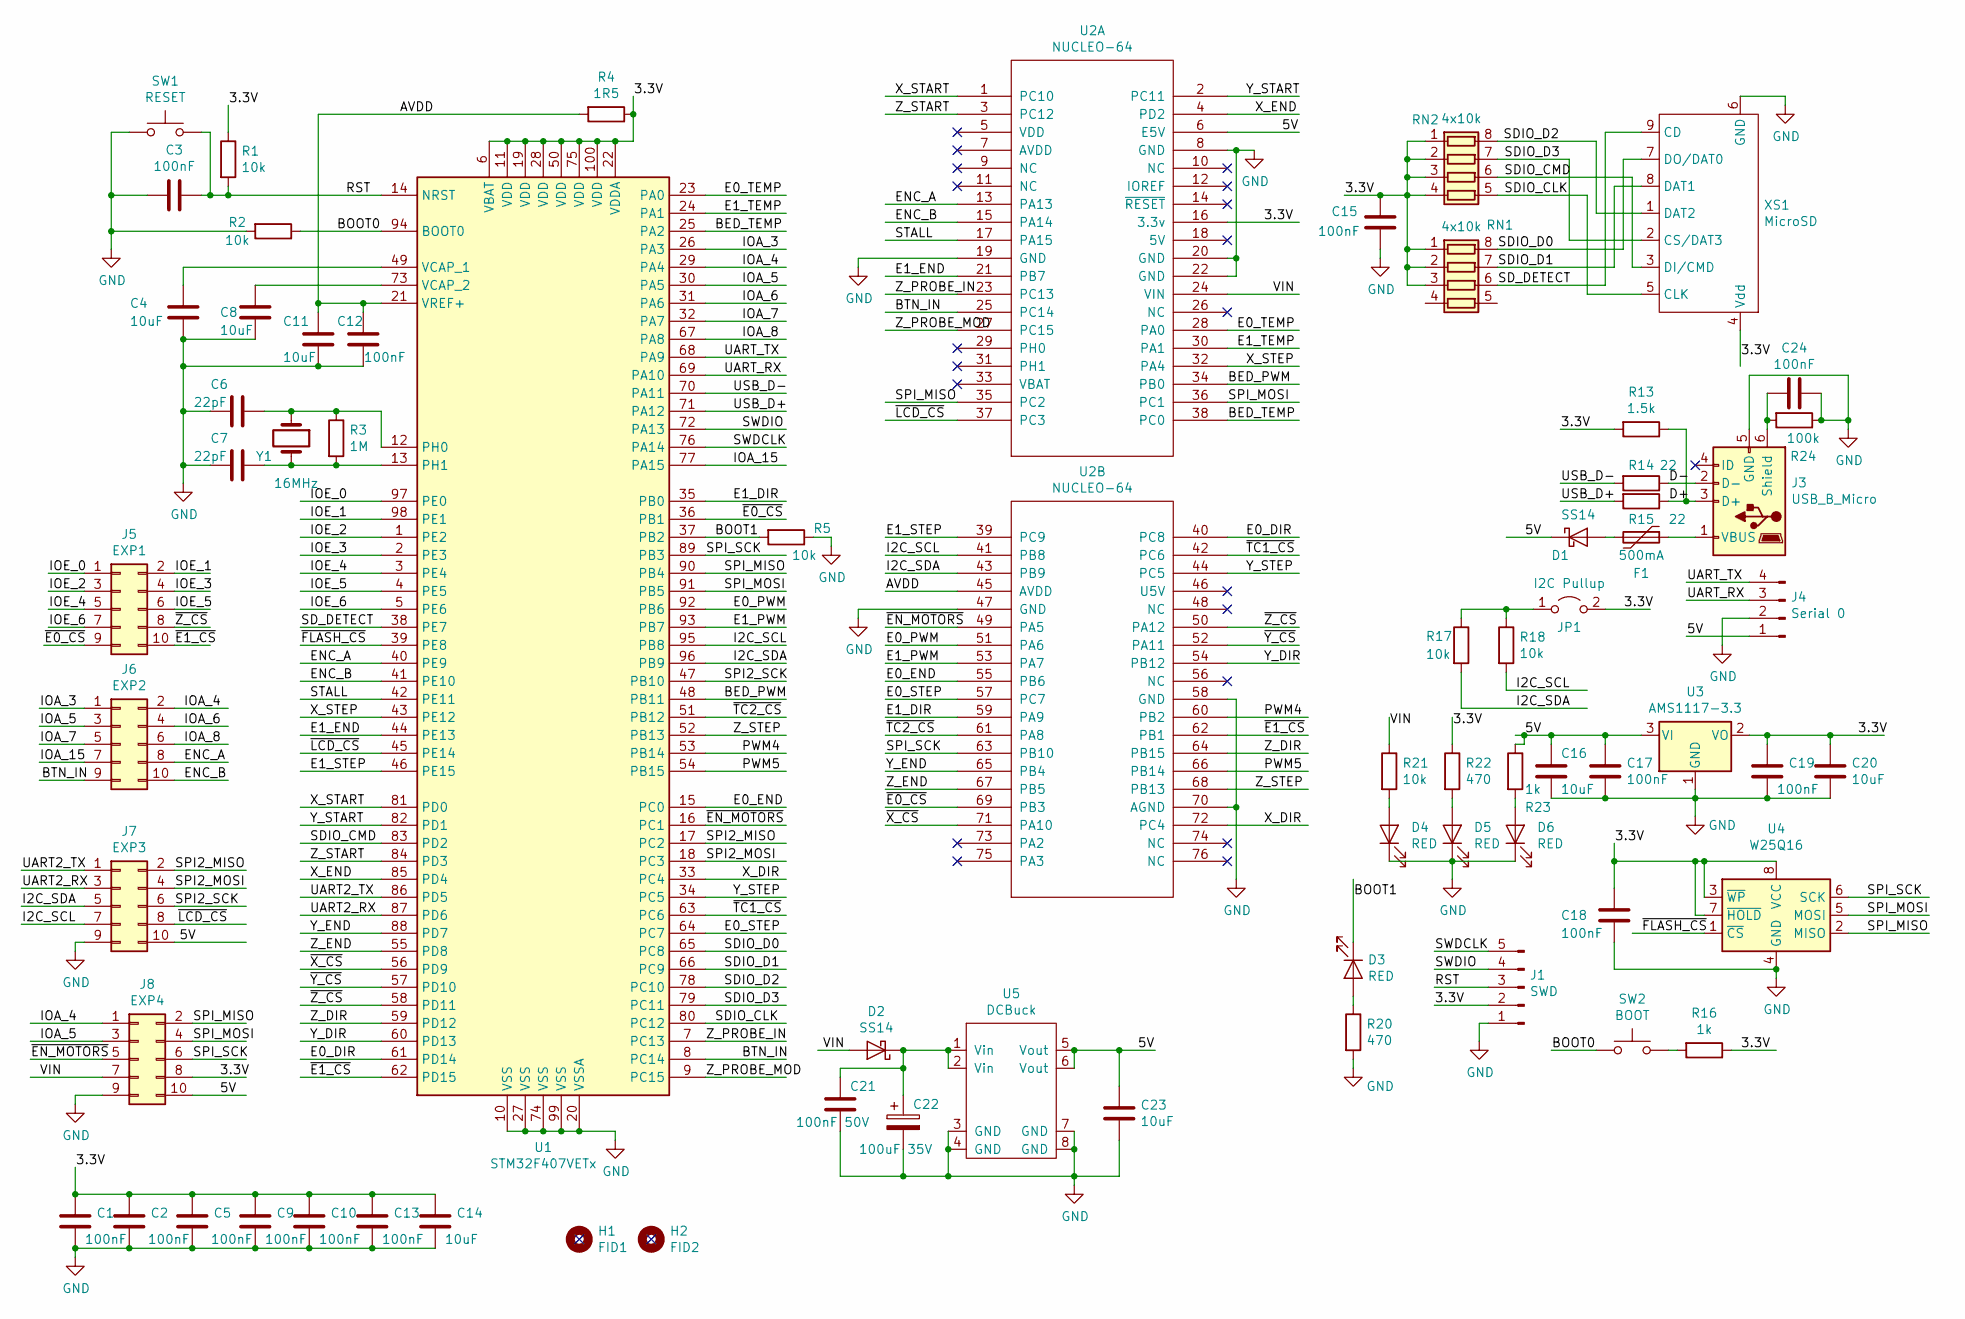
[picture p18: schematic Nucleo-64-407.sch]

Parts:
C1, C2, C3, C5, C9, C10, C12, C13, C15, C17, C18, C19, C24: 100nF; C_0603_1608Metric
C4, C8, C11, C14, C16, C20, C23: 10uF; C_0603_1608Metric
C6, C7: 22pF; C_0603_1608Metric
C21: 100nF 50V; C_0402_1005Metric
C22: 100uF 35V; CP_Elec_6.3x5.4
D1, D2: SS14; D_SMA
D3, D4, D5, D6: RED; D_0603_1608Metric
F1: 500mA; Fuse_0603_1608Metric
H1: FID1; Fiducial_1mm_Dia_2.54mm_Outer_CopperTop
H2: FID2; Fiducial_1mm_Dia_2.54mm_Outer_CopperTop
J1: SWD; PinHeader_1x05_P2.54mm_Vertical
J3: USB_B_Micro; MC-101C
J4: Serial 0; PinHeader_1x04_P2.54mm_Vertical
J5: EXP1; IDC-Header_2x05_P2.54mm_Vertical
J6: EXP2; IDC-Header_2x05_P2.54mm_Vertical
J7: EXP3; IDC-Header_2x05_P2.54mm_Vertical
J8: EXP4; IDC-Header_2x05_P2.54mm_Vertical
JP1: I2C Pullup; SolderJumper-2_P1.3mm_Open_TrianglePad1.0x1.5mm
R1, R2, R5, R17, R18, R21: 10k; R_0603_1608Metric
R3: 1M; R_0603_1608Metric
R4: 1R5; R_0603_1608Metric
R13: 1.5k; R_0603_1608Metric
R14, R15: 22; R_0603_1608Metric
R16, R23: 1k; R_0603_1608Metric
R20, R22: 470; R_0603_1608Metric
R24: 100k; R_0603_1608Metric
RN1, RN2: 4x10k; R_Array_Convex_4x0603
SW1: RESET; Button_4x4
SW2: BOOT; Button_4x4
U1: STM32F407VETx; LQFP-100_14x14mm_P0.5mm
U2: NUCLEO-64; Nucleo-64
U3: AMS1117-3.3; SOT-223-3_TabPin2
U4: W25Q16; SO-8_5.3x6.2mm_P1.27mm
U5: DCBuck; Buck2217
XS1: MicroSD; Conn_uSDcard
Y1: 16MHz; Crystal_SMD_HC49-SD

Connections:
/3.3V: C1.1, C2.1, C5.1, C9.1, C10.1, C13.1, C14.1, C15.1, C18.1, C19.1, C20.1, J1.2, J8.8, JP1.2 (B), R1.1, R4.1, R13.2, R16.1, R22.1, RN1.1 (R1.1), RN1.2 (R2.1), RN1.3 (R3.1), RN2.1 (R1.1), RN2.2 (R2.1), RN2.3 (R3.1), RN2.4 (R4.1), U1.6 (VBAT), U1.11 (VDD), U1.19 (VDD), U1.22 (VDDA), U1.28 (VDD), U1.50 (VDD), U1.75 (VDD), U1.100 (VDD), U2.16 (3.3v), U3.2 (VO), U4.3 (~WP), U4.7 (~HOLD), U4.8 (VCC), XS1.4 (Vdd)
/5V: C16.1, C17.1, C23.1, D1.1 (K), J4.1, J7.10, J8.10, R23.1, U2.6 (E5V), U3.3 (VI), U5.5 (Vout), U5.6 (Vout)
/AVDD: C11.1, C12.1, R4.2, U1.21 (VREF+), U2.45 (AVDD)
/BED_PWM: U1.48 (PB11), U2.34 (PB0)
/BED_TEMP: U1.25 (PA2), U2.38 (PC0)
/BOOT0: R2.1, SW2.1, U1.94 (BOOT0)
/BOOT1: D3.1 (K), R5.2, U1.37 (PB2)
/BTN_IN: J6.9, U1.8 (PC14), U2.25 (PC14)
/D+: J3.3 (D+), R13.1, R15.1
/D-: J3.2 (D-), R14.1
/E0_DIR: U1.61 (PD14), U2.40 (PC8)
/E0_END: U1.15 (PC0), U2.55 (PB6)
/E0_PWM: U1.92 (PB6), U2.51 (PA6)
/E0_STEP: U1.64 (PC7), U2.57 (PC7)
/E0_TEMP: U1.23 (PA0), U2.28 (PA0)
/E1_DIR: U1.35 (PB0), U2.59 (PA9)
/E1_END: U1.44 (PE13), U2.21 (PB7)
/E1_PWM: U1.93 (PB7), U2.53 (PA7)
/E1_STEP: U1.46 (PE15), U2.39 (PC9)
/E1_TEMP: U1.24 (PA1), U2.30 (PA1)
/ENC_A: J6.8, U1.40 (PE9), U2.13 (PA13)
/ENC_B: J6.10, U1.41 (PE10), U2.15 (PA14)
/I2C_SCL: J7.7, R18.2, U1.95 (PB8), U2.41 (PB8)
/I2C_SDA: J7.5, R17.2, U1.96 (PB9), U2.43 (PB9)
/IOA_3: J6.1, U1.26 (PA3)
/IOA_4: J6.2, J8.1, U1.29 (PA4)
/IOA_5: J6.3, J8.3, U1.30 (PA5)
/IOA_6: J6.4, U1.31 (PA6)
/IOA_7: J6.5, U1.32 (PA7)
/IOA_8: J6.6, U1.67 (PA8)
/IOA_15: J6.7, U1.77 (PA15)
/IOE_0: J5.1, U1.97 (PE0)
/IOE_1: J5.2, U1.98 (PE1)
/IOE_2: J5.3, U1.1 (PE2)
/IOE_3: J5.4, U1.2 (PE3)
/IOE_4: J5.5, U1.3 (PE4)
/IOE_5: J5.6, U1.4 (PE5)
/IOE_6: J5.7, U1.5 (PE6)
/PWM4: U1.53 (PB14), U2.60 (PB2)
/PWM5: U1.54 (PB15), U2.66 (PB14)
/RST: C3.1, J1.3, R1.2, SW1.2, U1.14 (NRST)
/SDIO_CLK: RN2.5 (R4.2), U1.80 (PC12), XS1.5 (CLK)
/SDIO_CMD: RN2.6 (R3.2), U1.83 (PD2), XS1.3 (DI/CMD)
/SDIO_D0: RN1.8 (R1.2), U1.65 (PC8), XS1.7 (DO/DAT0)
/SDIO_D1: RN1.7 (R2.2), U1.66 (PC9), XS1.8 (DAT1)
/SDIO_D2: RN2.8 (R1.2), U1.78 (PC10), XS1.1 (DAT2)
/SDIO_D3: RN2.7 (R2.2), U1.79 (PC11), XS1.2 (CS/DAT3)
/SD_DETECT: RN1.6 (R3.2), U1.38 (PE7), XS1.9 (CD)
/SPI2_MISO: J7.2, U1.17 (PC2)
/SPI2_MOSI: J7.4, U1.18 (PC3)
/SPI2_SCK: J7.6, U1.47 (PB10)
/SPI_MISO: J8.2, U1.90 (PB4), U2.35 (PC2), U4.2 (MISO)
/SPI_MOSI: J8.4, U1.91 (PB5), U2.36 (PC1), U4.5 (MOSI)
/SPI_SCK: J8.6, U1.89 (PB3), U2.63 (PB10), U4.6 (SCK)
/STALL: U1.42 (PE11), U2.17 (PA15)
/SWDCLK: J1.5, U1.76 (PA14)
/SWDIO: J1.4, U1.72 (PA13)
/UART2_RX: J7.3, U1.87 (PD6)
/UART2_TX: J7.1, U1.86 (PD5)
/UART_RX: J4.3, U1.69 (PA10)
/UART_TX: J4.4, U1.68 (PA9)
/USB_D+: R15.2, U1.71 (PA12)
/USB_D-: R14.2, U1.70 (PA11)
/VIN: D2.2 (A), J8.7, R21.1, U2.24 (VIN)
/X_DIR: U1.33 (PC4), U2.72 (PC4)
/X_END: U1.85 (PD4), U2.4 (PD2)
/X_START: U1.81 (PD0), U2.1 (PC10)
/X_STEP: U1.43 (PE12), U2.32 (PA4)
/Y_DIR: U1.60 (PD13), U2.54 (PB12)
/Y_END: U1.88 (PD7), U2.65 (PB4)
/Y_START: U1.82 (PD1), U2.2 (PC11)
/Y_STEP: U1.34 (PC5), U2.44 (PC5)
/Z_DIR: U1.59 (PD12), U2.64 (PB15)
/Z_END: U1.55 (PD8), U2.67 (PB5)
/Z_PROBE_IN: U1.7 (PC13), U2.23 (PC13)
/Z_PROBE_MOD: U1.9 (PC15), U2.27 (PC15)
/Z_START: U1.84 (PD3), U2.3 (PC12)
/Z_STEP: U1.52 (PB13), U2.68 (PB13)
/~E0_CS: J5.9, U1.36 (PB1), U2.69 (PB3)
/~E1_CS: J5.10, U1.62 (PD15), U2.62 (PB1)
/~EN_MOTORS: J8.5, U1.16 (PC1), U2.49 (PA5)
/~FLASH_CS: U1.39 (PE8), U4.1 (~CS)
/~LCD_CS: J7.8, U1.45 (PE14), U2.37 (PC3)
/~TC1_CS: U1.63 (PC6), U2.42 (PC6)
/~TC2_CS: U1.51 (PB12), U2.61 (PA8)
/~X_CS: U1.56 (PD9), U2.71 (PA10)
/~Y_CS: U1.57 (PD10), U2.52 (PA11)
/~Z_CS: J5.8, U1.58 (PD11), U2.50 (PA12)
GND: C1.2, C2.2, C3.2, C4.1, C5.2, C6.2, C7.2, C8.1, C9.2, C10.2, C11.2, C12.2, C13.2, C14.2, C15.2, C16.2, C17.2, C18.2, C19.2, C20.2, C21.2, C22.2, C23.2, C24.1, D4.1 (K), D5.1 (K), D6.1 (K), J1.1, J3.5 (GND), J4.2, J7.9, J8.9, R2.2, R5.1, R20.2, R24.1, SW1.1, U1.10 (VSS), U1.20 (VSSA), U1.27 (VSS), U1.74 (VSS), U1.99 (VSS), U2.8 (GND), U2.19 (GND), U2.20 (GND), U2.22 (GND), U2.47 (GND), U2.58 (GND), U2.70 (AGND), U3.1 (GND), U4.4 (GND), U5.3 (GND), U5.4 (GND), U5.7 (GND), U5.8 (GND), XS1.6 (GND)
unnamed: C4.2, U1.49 (VCAP_1)
unnamed: C6.1, R3.1, U1.12 (PH0), Y1.1
unnamed: C7.1, R3.2, U1.13 (PH1), Y1.2
unnamed: C8.2, U1.73 (VCAP_2)
unnamed: C21.1, C22.1, D2.1 (K), U5.1 (Vin), U5.2 (Vin)
unnamed: C24.2, J3.6 (Shield), R24.2
unnamed: D1.2 (A), F1.2
unnamed: D3.2 (A), R20.1
unnamed: D4.2 (A), R21.2
unnamed: D5.2 (A), R22.2
unnamed: D6.2 (A), R23.2
unnamed: F1.1, J3.1 (VBUS)
unnamed: JP1.1 (A), R17.1, R18.1
unnamed: R16.2, SW2.2


Board: 2 copper layers, 70.0 x 81.0 mm, 68 parts (0 on the bottom side), 103 nets.

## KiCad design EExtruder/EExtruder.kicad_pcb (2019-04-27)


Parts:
C1, C15: 10uF; C_0603_1608Metric
C2, C5, C6, C7, C17: 100nF; C_0603_1608Metric
C3, C4: 20pF; C_0603_1608Metric
C8, C9: 1uF; C_0603_1608Metric
C10, C16: 10nF; C_0603_1608Metric
FID1, FID2: Fiducial; Fiducial_1mm_Dia_2.54mm_Outer_CopperTop
H1, H2: MountingHole; MountingHole_3.2mm_M3
J1: 20A 50V; TerminalBlock_Phoenix_PT-1,5-2-3.5-H_1x02_P3.50mm_Horizontal
J2: AudioJack4; Jack_3.5mm_PJ320D_Horizontal
J11: Conn_01x03_Male; PinHeader_1x03_P2.54mm_Vertical
JP1: BOOT; PinHeader_1x02_P2.54mm_Vertical
JP2: SolderJumper_2_Open; SolderJumper-2_P1.3mm_Open_TrianglePad1.0x1.5mm
JP3, JP4: Jumper_3_Open; SolderJumper-3_P1.3mm_Open_Pad1.0x1.5mm
LCD1: Conn_02x06_Odd_Even; IDC-Header_2x06_P2.54mm_Vertical
PWM1, PWM2, PWM3, PWM4, PWM5: Conn_01x03_Male; PinHeader_1x03_P2.54mm_Vertical
PWM_PWR1: Conn_01x03_Male; PinHeader_1x03_P2.54mm_Vertical
R1, R2, R5, R6, R7: 10k; R_0603_1608Metric
R3: 0; R_0603_1608Metric
R4: 390; R_0603_1608Metric
R8: 1R5; R_0603_1608Metric
SWD1: Conn_01x05_Male; PinHeader_1x05_P2.54mm_Vertical
TC0, TC1: Conn_01x06_Male; PinHeader_1x06_P2.54mm_Vertical
U1: STM32F030C8Tx; LQFP-48_7x7mm_P0.5mm
U2: DCBuck; Buck2217
U3: AMS1117-3.3; SOT-223-3_TabPin2
Y1: 8MHz; Crystal_SMD_HC49-SD

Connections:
/3.3V: C1.1, C2.1, C5.1, C6.1, C17.1, JP1.1 (A), JP3.3 (B), JP4.3 (B), R1.1, R2.1, R5.1, R7.1, R8.2, SWD1.2, U1.1 (VDD), U1.24 (VDD), U1.48 (VDD), U3.2 (VO); also elsewhere on the board
/5V: C15.1, C16.1, JP3.1 (A), JP4.1 (A), U2.5 (Vout), U2.6 (Vout), U3.3 (VI)
/AVREF: C9.1, C10.1, R8.1, U1.9 (VDDA); also elsewhere on the board
/E0_FAN: U1.20 (PB2); also elsewhere on the board
/E1_FAN: U1.21 (PB10); also elsewhere on the board
/EXT1: LCD1.6, U1.33 (PA12)
/EXT2: LCD1.8, U1.40 (PB4)
/HEAT0: U1.13 (PA3); also elsewhere on the board
/HEAT1: U1.14 (PA4); also elsewhere on the board
/LCD_LED: LCD1.4, U1.41 (PB5)
/MISO: LCD1.5, TC0.3, TC1.3, U1.16 (PA6)
/MOSI: LCD1.3, TC0.4, TC1.4, U1.17 (PA7)
/PWM0: U1.18 (PB0); also elsewhere on the board
/PWM1: PWM1.1, U1.19 (PB1)
/PWM2: PWM2.1, U1.27 (PB14)
/PWM3: PWM3.1, U1.29 (PA8)
/PWM4: PWM4.1, U1.45 (PB8)
/PWM5: PWM5.1, U1.46 (PB9)
/SCL: J2.T, R2.2, U1.42 (PB6)
/SCL2: LCD1.2, R7.2, U1.35 (PF6)
/SDA: J2.R1, R1.2, U1.43 (PB7)
/SDA2: LCD1.1, R5.2, U1.36 (PF7)
/SPI_CLK: LCD1.7, TC0.5, TC1.5, U1.15 (PA5)
/SWCLK: SWD1.3, U1.37 (PA14)
/SWDIO: SWD1.4, U1.34 (PA13)
/TACH0: U1.26 (PB13); also elsewhere on the board
/TACH1: PWM1.2, U1.28 (PB15)
/TACH2: PWM2.2, U1.32 (PA11)
/TACH3: PWM3.2, U1.2 (PC13)
/TACH4: PWM4.2, U1.3 (PC14)
/TACH5: PWM5.2, U1.4 (PC15)
/TACH_E0: U1.38 (PA15); also elsewhere on the board
/TACH_E1: U1.39 (PB3); also elsewhere on the board
/TEMP0: U1.10 (PA0); also elsewhere on the board
/TEMP1: U1.11 (PA1); also elsewhere on the board
/TEMP_EX: LCD1.9, U1.12 (PA2)
/UART_RX: J11.2, U1.31 (PA10)
/UART_TX: J11.3, U1.30 (PA9)
/VIN: J1.1, LCD1.10, PWM_PWR1.1, PWM_PWR1.2, U2.1 (Vin), U2.2 (Vin); also elsewhere on the board
/~RESET: C7.1, SWD1.5, U1.7 (NRST)
/~TC0_CS: TC0.6, U1.22 (PB11)
/~TC1_CS: TC1.6, U1.25 (PB12)
GND: C1.2, C2.2, C3.2, C4.2, C5.2, C6.2, C7.2, C8.2, C9.2, C10.2, C15.2, C16.2, C17.2, J1.2, J11.1, JP2.2 (B), LCD1.11, PWM1.3, PWM2.3, PWM3.3, PWM4.3, PWM5.3, PWM_PWR1.3, R6.2, SWD1.1, TC0.2, TC1.2, U1.8 (VSSA), U1.23 (VSS), U1.47 (VSS), U2.3 (GND), U2.4 (GND), U2.7 (GND), U2.8 (GND), U3.1 (GND); also elsewhere on the board
unnamed: C3.1, R3.2, Y1.2
unnamed: C4.1, R4.2, Y1.1
unnamed: C8.1, JP4.2 (C), LCD1.12
unnamed: J2.R2, J2.S, JP2.1 (A)
unnamed: JP1.2 (B), R6.1, U1.44 (BOOT0)
unnamed: JP3.2 (C), TC0.1, TC1.1
unnamed: R3.1, U1.5 (PF0)
unnamed: R4.1, U1.6 (PF1)


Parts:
C11: 10uF 50V; C_1206_3216Metric
D1: RED; D_0603_1608Metric
D2: 1N4148; D_SOD-323_HandSoldering
J3: 6A 50V; TerminalBlock_Phoenix_PT-1,5-2-3.5-H_1x02_P3.50mm_Horizontal
Q1: DTC124E; SOT-23
Q2: PSMN7R0-30YL; LFPAK56
R9: 10k; R_0603_1608Metric
R10, R11, R12: 10K; R_0603_1608Metric

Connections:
/3.3V: R9.1; also elsewhere on the board
/HEAT0: Q1.1 (B), R9.2; also elsewhere on the board
/VIN: C11.1, D2.1 (K), J3.2, R10.2, R12.1; also elsewhere on the board
GND: C11.2, Q1.2 (E), Q2.1 (S), Q2.2 (S), Q2.3 (S), R11.2; also elsewhere on the board
unnamed: D1.1 (K), D2.2 (A), J3.1, Q2.5 (D)
unnamed: D1.2 (A), R12.2
unnamed: Q1.3 (C), Q2.4 (G), R10.1, R11.1

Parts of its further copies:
C12: 10uF 50V; C_1206_3216Metric
D3: RED; D_0603_1608Metric
D4: 1N4148; D_SOD-323_HandSoldering
J4: 6A 50V; TerminalBlock_Phoenix_PT-1,5-2-3.5-H_1x02_P3.50mm_Horizontal
Q3: DTC124E; SOT-23
Q4: PSMN7R0-30YL; LFPAK56
R13: 10k; R_0603_1608Metric
R14, R15, R16: 10K; R_0603_1608Metric

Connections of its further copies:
/3.3V: R13.1; also elsewhere on the board
/HEAT1: Q3.1 (B), R13.2; also elsewhere on the board
/VIN: C12.1, D4.1 (K), J4.2, R14.2, R16.1; also elsewhere on the board
GND: C12.2, Q3.2 (E), Q4.1 (S), Q4.2 (S), Q4.3 (S), R15.2; also elsewhere on the board
unnamed: D3.1 (K), D4.2 (A), J4.1, Q4.5 (D)
unnamed: D3.2 (A), R16.2
unnamed: Q3.3 (C), Q4.4 (G), R14.1, R15.1


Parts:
C13: 1uF; C_0603_1608Metric
D5: BAT54S; SOT-23
J5: Conn_01x02; PinHeader_1x02_P2.54mm_Vertical
R17: 4k7 1%; R_0603_1608Metric
R18: 10k; R_0603_1608Metric

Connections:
/AVREF: D5.2 (K), R17.1; also elsewhere on the board
/TEMP0: D5.3 (common), R18.1; also elsewhere on the board
GND: C13.2, D5.1 (A), J5.1; also elsewhere on the board
unnamed: C13.1, J5.2, R17.2, R18.2

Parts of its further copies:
C14: 1uF; C_0603_1608Metric
D6: BAT54S; SOT-23
J6: Conn_01x02; PinHeader_1x02_P2.54mm_Vertical
R19: 4k7 1%; R_0603_1608Metric
R20: 10k; R_0603_1608Metric

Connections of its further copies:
/AVREF: D6.2 (K), R19.1; also elsewhere on the board
/TEMP1: D6.3 (common), R20.1; also elsewhere on the board
GND: C14.2, D6.1 (A), J6.1; also elsewhere on the board
unnamed: C14.1, J6.2, R19.2, R20.2


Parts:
D7, D8: 1N4148; D_SOD-323_HandSoldering
J8: Conn_01x03_Male; PinHeader_1x03_P2.54mm_Vertical
Q5: SI2318CDS; SOT-23
R21, R23: 10k; R_0603_1608Metric
R22: 1k; R_0603_1608Metric

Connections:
/E0_FAN: R21.1, R22.2; also elsewhere on the board
/TACH_E0: D8.2 (A); also elsewhere on the board
/VIN: D7.1 (K), J8.2; also elsewhere on the board
GND: Q5.2 (S), R21.2; also elsewhere on the board
unnamed: D8.1 (K), R23.1
unnamed: Q5.1 (G), R22.1

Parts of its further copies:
D9, D10, D11, D12: 1N4148; D_SOD-323_HandSoldering
J7, J9: Conn_01x03_Male; PinHeader_1x03_P2.54mm_Vertical
Q6, Q7: SI2318CDS; SOT-23
R24, R26, R27, R29: 10k; R_0603_1608Metric
R25, R28: 1k; R_0603_1608Metric

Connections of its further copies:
/E1_FAN: R24.1, R25.2; also elsewhere on the board
/PWM0: R27.1, R28.2; also elsewhere on the board
/TACH0: D12.2 (A); also elsewhere on the board
/TACH_E1: D10.2 (A); also elsewhere on the board
/VIN: D9.1 (K), D11.1 (K), J7.2, J9.2; also elsewhere on the board
GND: Q6.2 (S), Q7.2 (S), R24.2, R27.2; also elsewhere on the board
unnamed: D10.1 (K), R26.1
unnamed: D11.2 (A), J9.1, Q7.3 (D)
unnamed: D12.1 (K), R29.1
unnamed: J9.3, R29.2
unnamed: Q6.1 (G), R25.1
unnamed: Q7.1 (G), R28.1

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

Board: 2 copper layers, 73.4 x 47.1 mm, 97 parts (0 on the bottom side), 71 nets.

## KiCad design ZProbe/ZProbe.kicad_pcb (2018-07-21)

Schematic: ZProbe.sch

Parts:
C1: 0.01uF; C_0603_1608Metric
C2: 0.1uF; C_0603_1608Metric
D1: 1N4148; D_SOD-323_HandSoldering
J1: SENSOR; PinHeader_1x03_P2.54mm_Horizontal
J2: Vin; JST_EH_B02B-EH-A_1x02_P2.50mm_Vertical
J3: Z-Probe; PinHeader_1x04_P2.54mm_Horizontal
Q1: DTA124E; SOT-23
Q2: DTC124E; SOT-23
R1: 1k; R_0603_1608Metric
R2: 10k; R_0603_1608Metric

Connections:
+5V: C2.1, J3.4, Q1.3, R2.1
GND: C1.2, C2.2, J1.1, J2.2, J3.2, Q2.2
unnamed: C1.1, D1.1 (K), R1.1
unnamed: D1.2 (A), Q1.1
unnamed: J1.2, R1.2
unnamed: J1.3, J2.1
unnamed: J3.1, Q2.3, R2.2
unnamed: Q1.2, Q2.1


Board: 2 copper layers, 23.5 x 13.5 mm, 10 parts (0 on the bottom side), 8 nets.

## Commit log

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2018-03-26 Add 3 axis and 2 extruders. Basic thermistor temperature sensing and MOSFET heaters in the extruders.
    [AxisControl.sch, BasicHeater.sch, DualMotorConnect.sch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]
2018-03-26 Added the rest of the printer parts. Should be complete more or less.
    [AxisControl.sch, BasicHeater.sch, DualMotorConnect.sch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]
2018-04-02 Finish the schematics. All pins are assinged to the NUCLEO-64 board.
    [AxisControl.sch, BasicHeater.sch, DualMotorConnect.sch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]
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2018-04-05 Assigned footprints for all components. Inductors are approximate size. MOSFETs dont agree with the footprints. Saved pcb netlist report as report.txt.
    [AxisControl.sch, BasicHeater.sch, BedHeater.sch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]
2018-04-06 Updated components. Removed power supply. Component layout on PCB.
    [AxisControl.sch, BasicHeater.sch, BedHeater.sch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]
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2018-04-08 Added mounting holes and fiducials. Placed all components labels so they are readable.
    [BasicHeater.sch, Endstop.sch, Extruder.sch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]
2018-04-08 Hmm price is too expencive for this board. Looking to reduce the specs to 6/6 mil spacing .3mm via drills.
    [PrntrBoardV1.kicad_pcb]
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2018-04-08 Placer all on 10x10 board. All labels are readable. Added connector text.
    [PrntrBoardV1.kicad_pcb]
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2018-04-08 Added drive power pours for the motor connections. Added vias to the outer poors.
    [PrntrBoardV1.kicad_pcb]
2018-04-08 Added copper pours for the inner driver motor connectors on layer 2.
    [PrntrBoardV1.kicad_pcb]
2018-04-08 Complete the drivers power pours on layer 3.
    [PrntrBoardV1.kicad_pcb]
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2018-04-08 Re-worked motor protection capacitors, so they don't take space from the copper pours for the driver output pins.
    [PrntrBoardV1.kicad_pcb]
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2018-04-09 Make the high voltage bar thicker onthe extruder side.
    [PrntrBoardV1.kicad_pcb]
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2018-04-09 Added 3D model of the nucleo board. Created a few screenshots from the 3D viewer.
    [PrntrBoardV1.kicad_pcb]
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2018-04-16 Switched to local foorprints for terminals and LED. Switched to local foorprint for the printer driver ship - it has larger thermal pad ares.
    Placement V1 complete.
    [BasicHeater.sch, BedHeater.sch, Endstop.sch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]
2018-04-16 Moved labels around. All should be visible and readable. (for now).
    [PrntrBoardV1.kicad_pcb]
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2018-04-17 Routed power stage for extruders and heater controls. Routed some easy connections.
    [PrntrBoardV1.kicad_pcb]
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2018-04-19 Locked vias on power pads for the drivers.
    [PrntrBoardV1.kicad_pcb]
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2018-04-20 Changed vias on the AVREF net, they were too big.
    [PrntrBoardV1.kicad_pcb]
2018-04-20 Straighten come lines, re-route heater power. Add heater mosfet pours on the bottom layer.
    [PrntrBoardV1.kicad_pcb]
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2018-05-04 Movet top FID to the top right corner. Added PCB origin. Switched 0.1uF 50V cpas to 0402 size.
    [AxisControl.sch, Endstop.sch, Extruder.sch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]
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2018-05-10 Added 10k pullups to control inputs for heaters, to disable heaters when control module is not installed.
    [Endstop.sch, FanControl.sch, PrntrBoardV1.kicad_pcb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]
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2018-05-12 Removed SD_MODE wire. Added motor clock oscillator. Wired the clock on the internal layer to reduce EMI.
    [AxisControl.sch, Endstop.sch, Extruder.sch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]
2018-05-13 Re-routed the extruder motor controls, so there is a large area on the bottom to disipate the IC heat.
    [PrntrBoardV1.kicad_pcb]
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2018-05-13 Re-route the axis extruder so the bottom plate has more space to dissipate heat.
    [PrntrBoardV1.kicad_pcb]
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2018-05-14 Change the LCD power to 5V, keep the 3.3V only for the backlight LED.
    [PrntrBoardV1.kicad_pcb, PrntrBoardV1.sch, ST7735 LCD.sch]
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2018-05-25 Fix small routing issues.
    [PrntrBoardV1.kicad_pcb]
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2018-05-28 Added dual themocouple pins. You'll have to sacrifice the controllable extruder cooling fans via jumpers.
    [FanControl.sch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]
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2018-06-21 Added filter capacitors on the 3.3v as well as the AVREF power inputs.
    [Endstop.sch, PrntrBoardV1.kicad_pcb, PrntrBoardV1.sch]
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2018-07-02 Fix endstops.
    [AxisControl.sch, Endstop.sch]
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2018-07-04 Fix endstops. Add extra fan connectors. Start routing motors drivers.
    [AxisControl.sch, Endstop.sch, MotorConnect.sch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]
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2018-07-15 Minor improvements to the layout - leave more clearance around the motor connectors.
    [PrntrBoardV1-B.Cu.gbl, PrntrBoardV1-B.Mask.gbs, PrntrBoardV1-B.Paste.gbp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]
2018-07-18 Increase the size of some vias. Increase the size of the 3V trace to the drivers. Make labels more readable.
    [PrntrBoardV1-F.Paste.dxf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]
2018-07-20 Added heatsink labels on the bottom. Moved electrolytic caps around to make more clearance for top heatsink(s). Moved extra fan connectors around. Increased VIA spacing on driver bus connectors. Fixe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
    [PrntrBoardV1-B.Cu.gbl, PrntrBoardV1-B.Mask.gbs, PrntrBoardV1-B.Paste.gbp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]
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2018-07-31 Started rev 3. Added encoder iand button input. Re-routed LCD A0 and RESET to be connected to the HW I2C pins.
    [Extruder.sch, MotorConnect.sch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]
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2018-08-05 Rellocate internal fan connectors, so they are out of the way of the nucleo board. Removed all footprint references from the silk screen.
    [PrntrBoardV1-B.Cu.gbl, PrntrBoardV1-B.Mask.gbs, PrntrBoardV1-B.Paste.gbp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]
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2018-08-05 Update 3D models for the connectors. Remove the nucleo-64 3D model fron the pcb file - it was loading very slow. Generate board 3D model.
    [PrntrBoardV1.kicad_pcb]
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2018-08-12 Switch away from rounded rect pads. The PCB boar house had issues making the board.
    [BasicHeater.sch, BedHeater.sch, Endstop.sch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]
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2018-08-26 Increase board revision. Add one more layer of connection for the heated bed power pin.
    [PrntrBoardV1-B.Cu.gbl, PrntrBoardV1-B.Mask.gbs, PrntrBoardV1-B.Paste.gbp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]
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2018-10-14 Select correct terminals. Use old style square footprints.
    [EExtruder.kicad_pcb, EExtruder.sch, FanCtl.sch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]
2018-10-14 Add solder jumper on the audio jack to avoid ground loops.
    [EExtruder.kicad_pcb, EExtruder.sch, Heater.sch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]
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2018-11-23 Add custom NUCLEO-64 replacement based on F407VE.
    [Nucleo-64-407.kicad_pcb, Nucleo-64-407.sch]
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2019-01-13 Added 3.3V LDO, updated TC connectors to 6 pins. Re-arranged the layout.
    [EExtruder-B_Cu.gbl, EExtruder-B_Mask.gbs, EExtruder-B_Paste.gbp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]
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2019-01-27 Fix capavitor value.
    [Nucleo-64-407.sch]
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2019-05-12 Fix bugs when upgrading KiCAD versions.
    [AxisControl.sch, BasicHeater.sch, BedHeater.sch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]
2019-05-19 Updated power LED locations. Updated aux power connector locations. Updated fan voltage select location. Moved all fan connecters to make room for fan voltage selector. Updated all silk screen to use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
    [Nucleo-64-407-B_Cu.gbl, Nucleo-64-407-B_Mask.gbs, Nucleo-64-407-B_Paste.gbp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]
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2019-06-23 Update a few footprints so the origin of the footpring is in teh center.
    [Nucleo-64-407.kicad_pcb]
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2019-08-26 Minor updates to the nucleo-64 board. Added more signals to the extension headers. Use resistor networks. Fix diode footprint.
    [Nucleo-64-407-B_Cu.gbl, Nucleo-64-407-B_Mask.gbs, Nucleo-64-407-B_Paste.gbp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]
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2019-08-31 Avoid using 3.3V only pins for IO board.
    [IOBoard-B_Cu.gbl, IOBoard-B_Mask.gbs, IOBoard-B_Paste.gbp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]
2019-09-02 Add reverse power protection to the nucleo board.
    [IOBoard.kicad_pcb, Nucleo-64-407.kicad_pcb, Nucleo-64-407.sch]
2019-09-16 New reveision of the IO board, correct LCD_EN signal.
    [IOBoard-B_Cu.gbl, IOBoard-B_Mask.gbs, IOBoard-B_Paste.gbp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]
2020-05-02 Fix bug in the TMC2130 driver schematics.
    [AxisControl.sch, BasicHeater.sch, BedHeater.sch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]
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
